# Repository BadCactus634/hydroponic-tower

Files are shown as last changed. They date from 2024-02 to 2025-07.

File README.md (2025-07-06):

ENGLISH USERS [READ HERE](english.md)!

ATTENZIONE!! AGGIORNAMENTO CIRCUITO: Il convertitore DC-DC va messo PRIMA del relè, altrimenti l'ESP si riavvierà quando quest'ultimo scatta. Questo a causa di un momentario undervoltage che si può correggere inserendo un condensatore.

# Serra idroponica
Crea una serra idroponica stampata in 3D con Arduino/ESP32!  



## Overview
Questa serra idroponica modulare è stata interamente stampata in 3D utilizzando del [PLA della PolyTerra](https://amzn.eu/d/4JCfyR1). Per stampare i pezzi marroni ho utilizzato poco meno di 1kg di filamento, mentre per quelli verdi circa 400g.  
C'è da dire però che **non ho avuto stampe fallite** e che **tutti i modelli sono stati ridotti del 10%** perché non ci stavano sul piatto della mia stampante (Flsun Q5).  
Se non l'hai ancora fatto, clicca qui (WIP!) per vedere il video che ho fatto dove mostro la serra in generale e spiego come l'ho costruita.

Questi sono alcuni dei componenti stampati:  

 <br>

Lista della spesa:
- 1kg filamento marrone
- 1kg filamento verde
- stampante 3D (ovviamente)
- pompa 12V
- ESP32/Arduino (qualsiasi)
- sensore di livello dell'acqua
- un vaso (se non è presente nei modelli già fatti, devi crearti un modello del coperchio su misura)
- nutrimento per coltivazioni idroponiche
- piantine da mettere nella serra
- step-up 5V-12V
- potenziometro, cavi, LED
 
Opzionale:
- millefori, stagno, stagnatore
- sensori per pH, CE e temperatura dell'acqua (io non li ho usati)

## Modelli 3D
I modelli che ho utilizzato io e che vedi nel mio video li trovi tutti nella cartella **File STL utilizzati**, inclusa la scatoletta che contiene i componenti.  
Non c'è il file del coperchio del vaso perché l'ho costruito in legno, visto che il mio vaso aveva delle misure particolari.

Nel caso ti servissero puoi scaricare lo zip contenente i modelli originali cliccando [qui](https://t.me/makersITA/907372) (non ci sono più su Thingiverse).

## Circuito
ATTENZIONE!! IL CIRCUITO NON E' STABILE: Il convertitore DC-DC va messo PRIMA del relè, altrimenti l'ESP si riavvierà quando scatta il relè. Credo sia a causa di un momentario undervoltage. 

Il cuore di questo progetto è un semplicissimo **ESP32** che fa da timer che accende la pompa dell'acqua per 5 minuti e poi attende un tempo variabile (regolabile dal potenziometro) che può andare da 10 a 60 minuti.  
Ci sono due LED che indicano lo stato del sistema (verde acceso = pompa attiva; rosso lampeggiante = mancanza di acqua nel serbatoio).  
L'ESP32 attiva un relè tramite un transistor, e il relè a sua volta attiva uno step-up che converte i 5V dell'alimentazione a 12V per la pompa dell'acqua, accendendola.  
Lo step-up è stato collegato a valle del relè in modo da essere attivato solo quando la pompa deve essere alimentata, risparmiando qualche mA del circuito di conversione e allungando quindi la durata della batteria (anche se io lo alimento tramite un alimentatore a muro).  

  

Nella figura sotto è riportato lo schema del circuito.

***ATTENZIONE!! È importante collegare il potenziometro al pin 33 (che corrisponde all'ADC1) perchè se lo colleghiamo a uno dei pin dell'ADC2 non funzionerà l'integrazione con Arduino Cloud, visto che l'ADC2 non funziona se la scheda utilizza il WiFi.***  

Circuito_schema

## Codice
Il codice è nel file **Codice_SerraIdroponica.ino** e questo è il suo funzionamento di base:  
- C'è acqua nel serbatoio?  
  Allora se è passato il tempo di attesa (regolabile tramite potenziometro da 10min a 60min) attiva la pompa per 5min.
  Durante il tempo di attivazione della pompa (che funziona tramite millis) verifica ogni secondo se è ancora presente acqua nel serbatoio, altrimenti fermala.

## Integrazione con Arduino Cloud 
Se volete fare l'integrazione su Arduino Cloud dovete usare il codice nella cartella **Codice_ArduinoCloud** perché ci sono alcune modifiche rispetto al codice normale.
Inoltre, sempre su Arduino Cloud, vanno impostate le seguenti variabili:  

   

**ATTENZIONE**  
I pin in entrambe le versioni del codice e lo schema del circuito si riferiscono alla scheda ESP32. Se volete utilizzare un Arduino dovete modificare i pin nel codice e nel circuito.

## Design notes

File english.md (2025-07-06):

WARNING!! THIS CIRCUIT IS NOT STABLE: The DC-DC converter needs to be put BEFORE the relay, otherwise an undervoltage would occur, resetting the ESP. There is a need for a capacitor.

# Hydroponic tower
Create a 3D-printed hydroponic tower with Arduino/ESP32!  



## Overview
This hydroponic tower has been entirely 3D printed using [PolyTerra PLA](https://amzn.eu/d/4JCfyR1). In order to print the brown modules I used almost 1kg of filament, whereas for the green ones I used 400g.  
It has to be sayd tho, that I **haven't got any failed print** and **all models were reduced by 10%** because they won't fit in my printing plate (I have an Flsun Q5).  
You can see a video of me building it (WIP). Note: it's in italian.

These are some of the printed components:  

 <br>

Shopping list:
- brown filament 1kg
- green filament 1kg
- 3D printer (obiuvsly)
- 12V water pump
- ESP32/Arduino (any)
- water level sensor
- vase cover (if yours isn't in the premade models, you need to create one custom-made)
- water nutriments for hydroponic based coltivations
- plants
- step-up 5V-12V
- potentiometer, cables, LEDs
 
Optional:
- prepboard, solder, soldering iron
- pH, CE and water temperature sensors (I haven't used them)

## 3D models
You can find all the models I used in the **File STL utilizzati** directory, including the box on which I putted the components.  
I haven't included the custom-made file for my vase cover because I builded it using wood.

If you need the original models, you can find them [here](https://t.me/makersITA/907372) (they aren't on Thingiverse anymore).

## Circuit
WARNING!! THIS CIRCUIT IS NOT STABLE: The DC-DC converter needs to be put BEFORE the relay, otherwise an undervoltage would occur, resetting the ESP. 

The heart of this project is a simple **ESP32** used as a timer, that turns on the water pump for 5 minutes and then waits a variable time that we can specify using the potentiometer (from 10 to 60 minutes).    
There are 2 LEDs that indicate the status of the system (green on = pump active; red blinking = no water).  
The ESP32 is connected to a relè via a transistor, the relè triggers a step-up that converts the 5V from the USB cable up to 12V for the water pump, thus turning it on.  
The step-up is connected after the relè, so it's only activated when the pump needs to be on, thus earning some mA for battery life, if you decide to power the system that way.  



You can see the circuit diagram in the picture below.  

***ATTENTION!! It's important to connect the potentiometer to pin 33 (which corresponds to ADC1) because if we were to connect it to any ADC2 pin, the integration with Arduino Cloud won't work, as the ADC2 doesn't work if the board is using WiFi.***

Circuito_schema

## Code
The code is in the file **Codice_SerraIdroponica.ino** and this is it's base working scheme:  
- Is there any water in the vase?  
  Then if the wait time has expired, activates the pump for 5min.  
  During pump activation time (it works by using millis) verify every second if water is still present in the vase, if not, stop the pump and turn on the red LED.

## Arduino Cloud integration 
If you want to integrate Arduino Cloud, you need to use the code in the directory **Codice_ArduinoCloud** because the code needs to be modified a bit.  
You also need to setup those variables in Arduino Cloud:  

   
  
**ATTENTION**  
The pins in the code and in the circuit diagram refers to the ESP32 board. If you want to use an Arduino you need to edit them in the code and thus in the circuit.

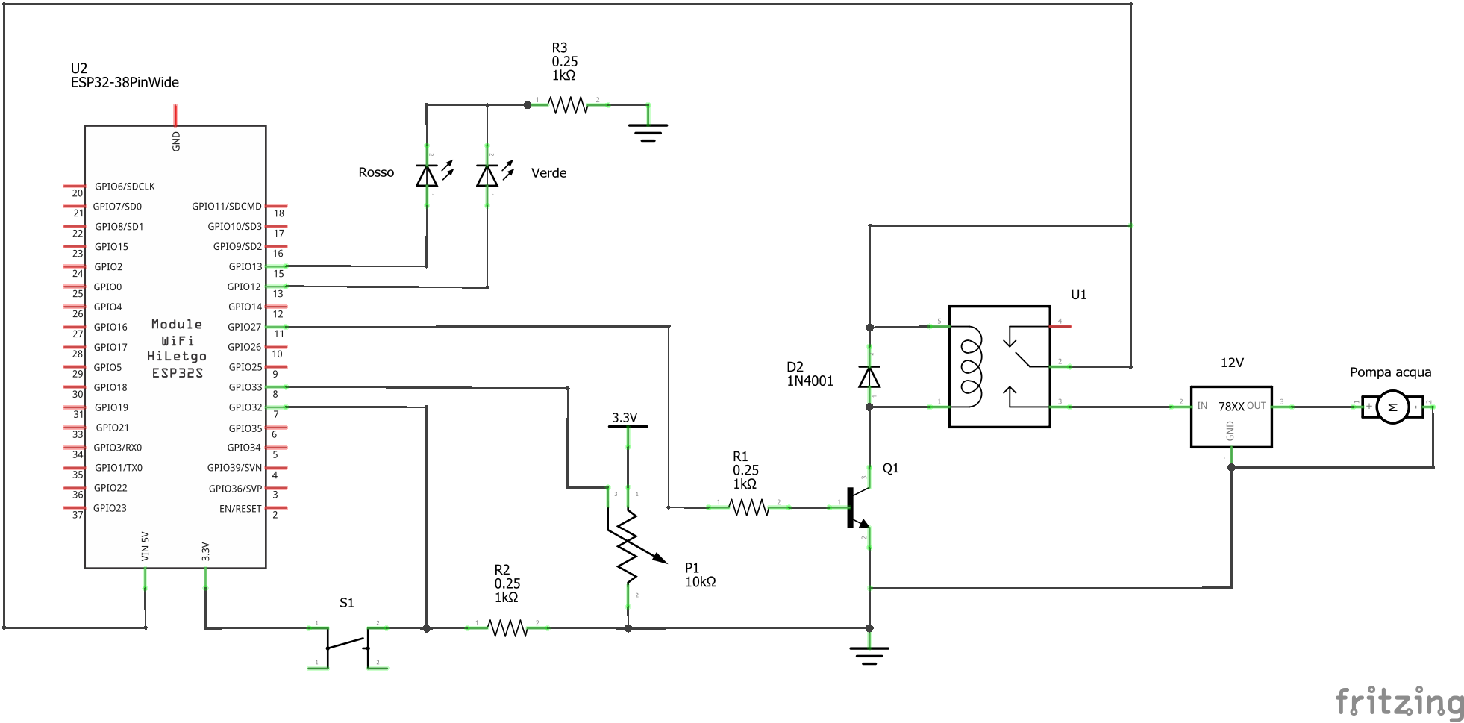
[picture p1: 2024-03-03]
Circuito_schema.png

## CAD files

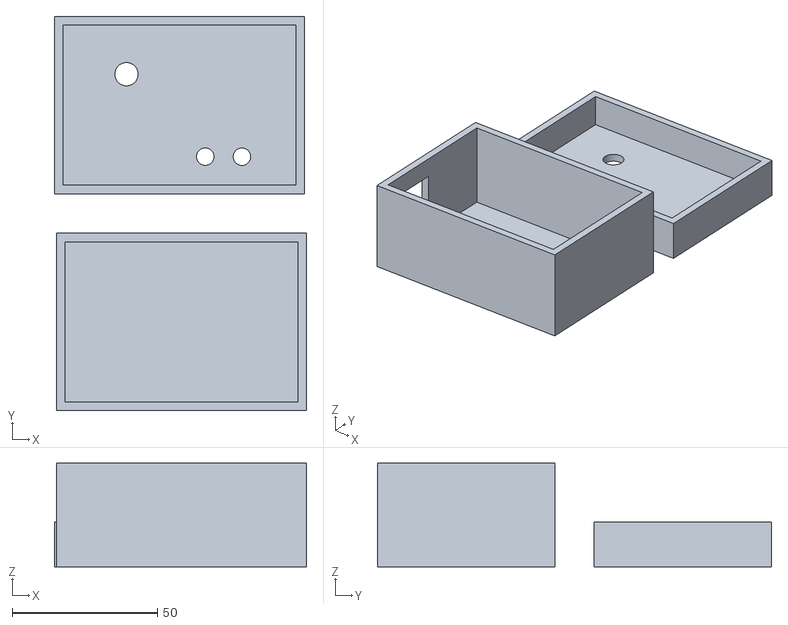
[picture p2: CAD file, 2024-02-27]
File STL utilizzati/Scatola componenti.stl
86.7 x 135.4 x 35.7

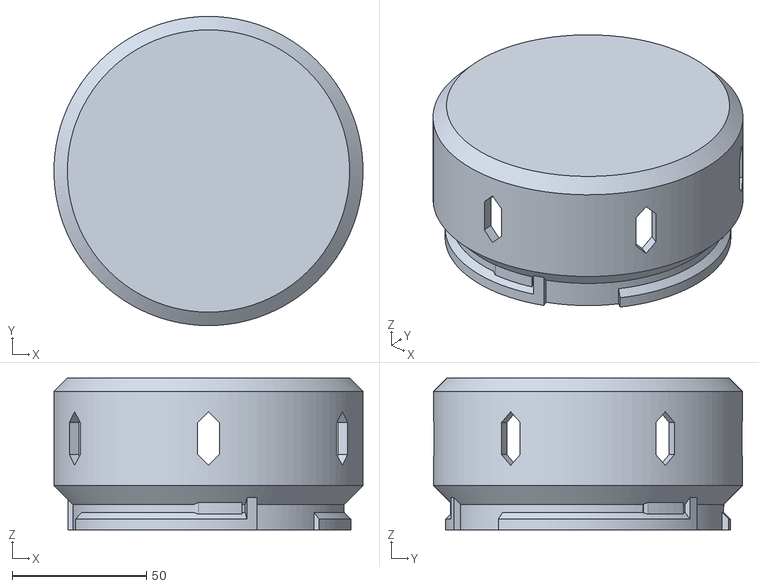
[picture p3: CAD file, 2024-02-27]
File STL utilizzati/Lid.STL
114.9 x 115.0 x 56.5

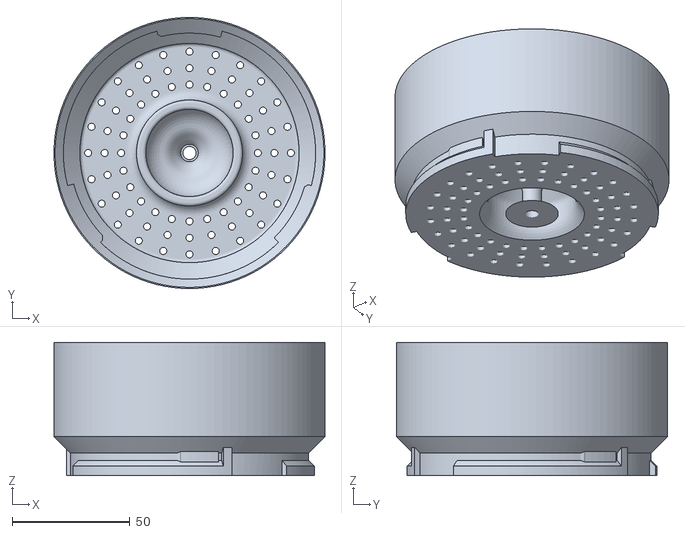
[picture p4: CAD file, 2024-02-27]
File STL utilizzati/Inserto superiore EU.stl
114.9 x 115.0 x 56.5

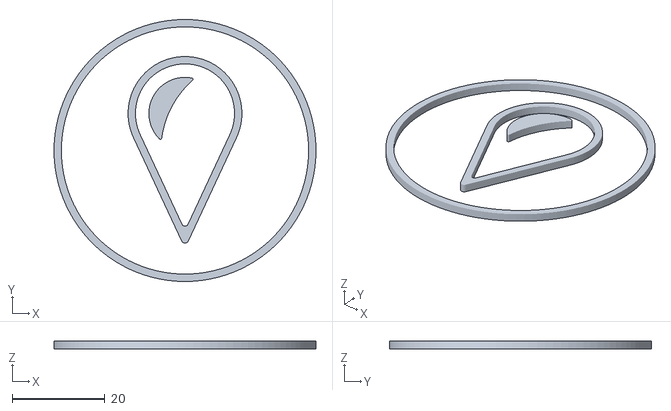
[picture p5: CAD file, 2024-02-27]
File STL utilizzati/Filling_Cap_Symbol.STL
56.6 x 56.6 x 1.70

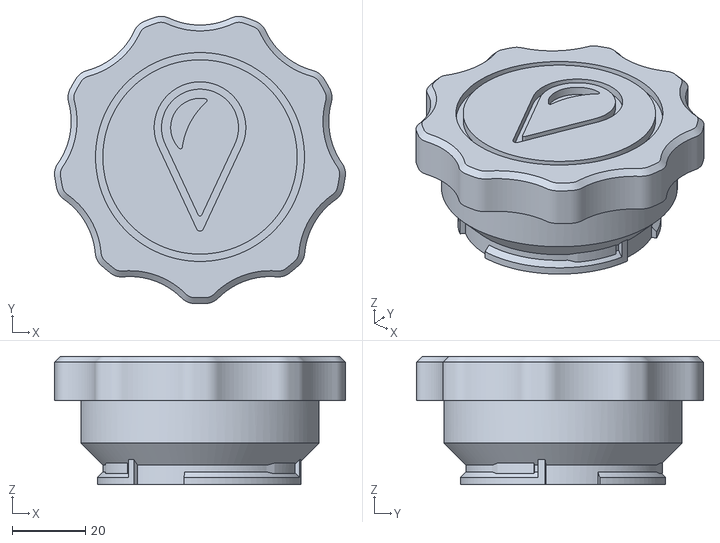
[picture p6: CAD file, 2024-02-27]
File STL utilizzati/Filling_Cap.STL
79.4 x 78.4 x 35.0

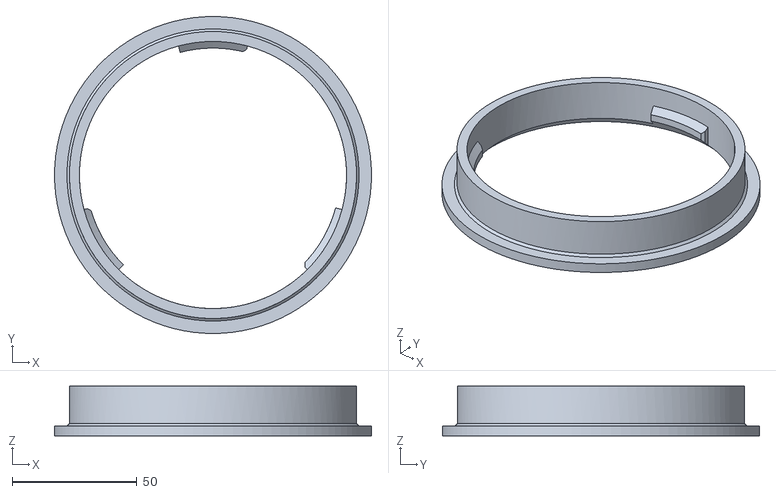
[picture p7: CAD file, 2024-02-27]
File STL utilizzati/Module_Adapter.STL
127.0 x 127.0 x 20.0

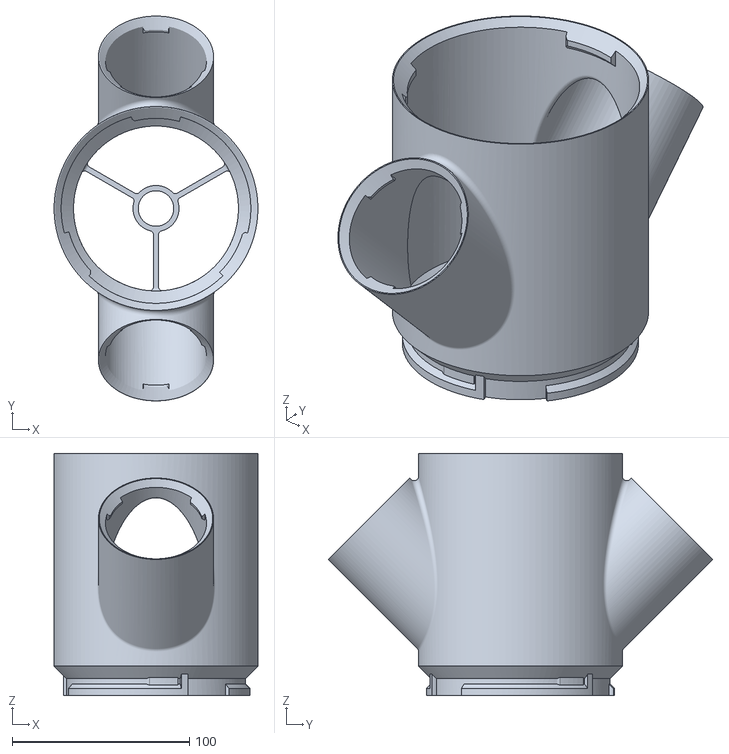
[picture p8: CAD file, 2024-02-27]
File STL utilizzati/2-Way_Planting_Module_Hollow_Opposite.STL
114.9 x 217.1 x 136.5

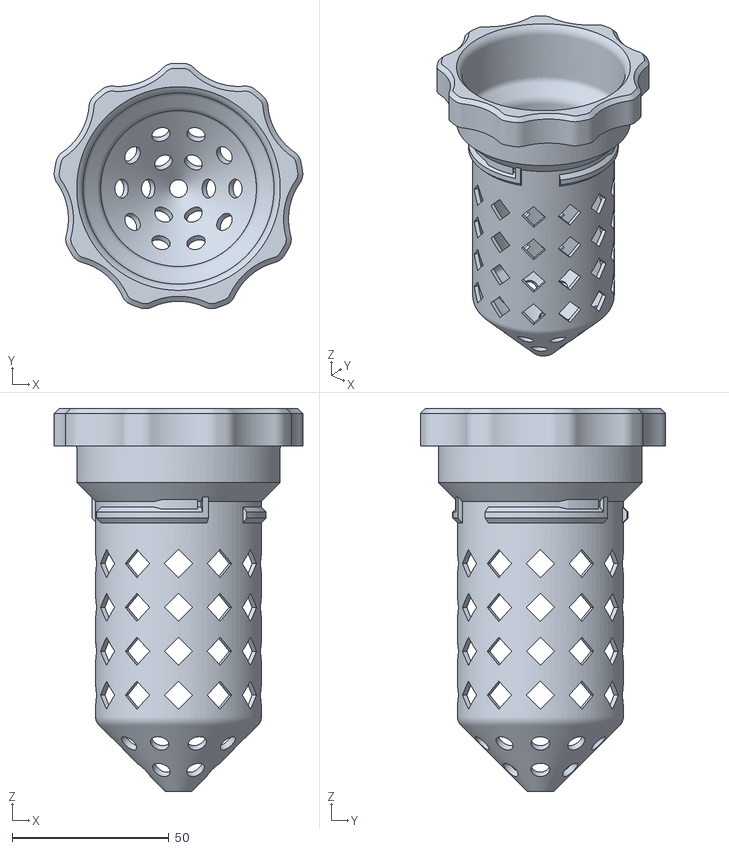
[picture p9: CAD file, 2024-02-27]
File STL utilizzati/Standard_Pot_02.STL
79.4 x 78.4 x 122.3

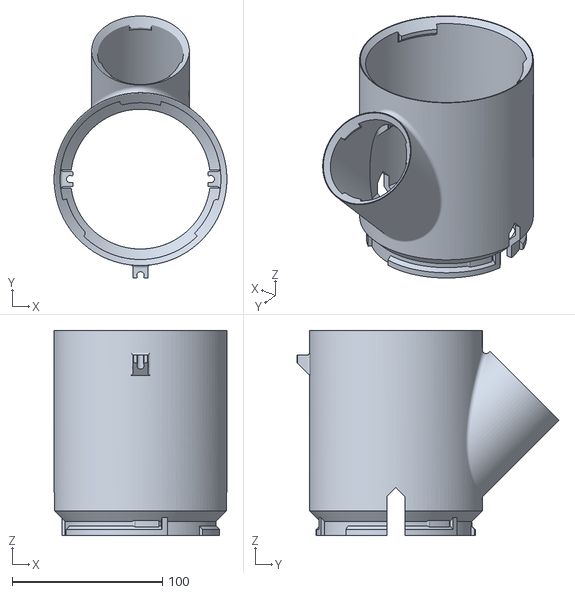
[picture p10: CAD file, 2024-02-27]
File STL utilizzati/Filling_Module_Cut_mod_01.STL
115.0 x 174.3 x 136.5

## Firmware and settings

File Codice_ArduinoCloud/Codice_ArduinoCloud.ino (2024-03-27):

#include "thingProperties.h"

int sensore = 32; // Sensore
int pompa = 27; // Pompa
int ledV = 12; // LED verde
int ledR = 13; // LED rosso
int potenziometro = 33, pausa = 0, nuovaPausa = 0;
bool halt;

unsigned long vecchioMillis, nuovoMillis, nuovoMillisHalt, vecchioMillisHalt;

// Temporizzazioni
int minuto = 60000; // Durata di 1 minuto (default: 60000)

// int tPompa = 5; // La pompa si accenderà per questo numero di minuti
int tMin = 10;
int tMax = 60;

void setup() {
  // Initialize serial and wait for port to open:
  Serial.begin(9600);
  // This delay gives the chance to wait for a Serial Monitor without blocking if none is found
  delay(1500); 

  // Defined in thingProperties.h
  initProperties();

  // Connect to Arduino IoT Cloud
  ArduinoCloud.begin(ArduinoIoTPreferredConnection);
  
  setDebugMessageLevel(2);
  ArduinoCloud.printDebugInfo();
  
  
  pinMode(sensore, INPUT);
  pinMode(pompa, OUTPUT);
  pinMode(ledV, OUTPUT);
  pinMode(ledR, OUTPUT);

  digitalWrite(ledV, LOW);
  digitalWrite(ledR, LOW);
  digitalWrite(pompa, LOW);
  
  pausa = analogRead(potenziometro);
  delay(100); // Delay per ADC
  pausa = map(pausa, 0, 4095, tMin, tMax);
  tempoRimanenteHalt = pausa;
  
  delay(2000);
  
  vecchioMillis=millis();
  tPompa = 5;
}

void loop() {
  ArduinoCloud.update();
  
  nuovaPausa = analogRead(potenziometro);
  delay(100); // Delay per ADC
  nuovaPausa = map(nuovaPausa, 0, 4095, tMin, tMax);

  if(nuovaPausa!=pausa){
    pausa=nuovaPausa;
    tempoRimanenteHalt = pausa;
  }
  
  if(digitalRead(sensore)) { // Se c'è acqua
      presenzaAcqua=true;
      
      if(!halt)
        controlloPompa();
    
  } else { // Se non c'è acqua
    vecchioMillis = millis();
    halt=false;
    timerPompa = 0;
    digitalWrite(pompa, LOW);
    digitalWrite(ledV, LOW);
    statoPompa=false;
    presenzaAcqua=false;
    
    
    digitalWrite(ledR, HIGH);
    delay(600);
    digitalWrite(ledR, LOW);
    delay(600);
  }
  
  delay(1000);
  
  if(halt){
    nuovoMillisHalt=millis();
    tempoRimanenteHalt = pausa - (nuovoMillisHalt - vecchioMillisHalt)/minuto;
    if(nuovoMillisHalt - vecchioMillisHalt >= pausa*minuto){
      halt=false;
      tempoRimanenteHalt = pausa;
      vecchioMillis = millis(); 
    }
  }
  
}


void controlloPompa(){
  nuovoMillis = millis();
  digitalWrite(pompa, HIGH);
  digitalWrite(ledV, HIGH);
  timerPompa = tPompa - (nuovoMillis - vecchioMillis)/minuto; // Tempo attività pompa rimanente
  statoPompa=true;

  if(nuovoMillis - vecchioMillis >= tPompa*minuto){ // Se è finito il tempo di attività della pompa
    digitalWrite(pompa, LOW);
    digitalWrite(ledV, LOW);
    timerPompa = 0;
    statoPompa = false;
    halt = true;
    vecchioMillisHalt=millis();
  }
}



/*
  Since TPompa is READ_WRITE variable, onTPompaChange() is
  executed every time a new value is received from IoT Cloud.
*/
void onTPompaChange()  {
  // Add your code here to act upon TPompa change
}

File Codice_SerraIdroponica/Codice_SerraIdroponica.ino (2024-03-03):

/* NATMUS
 *  by Stefano Rossi - 28/02/2024
 *  
 *  - Serra idroponica -
 *  questo codice non include la gestione dei sensori di parametri
 *  avanzati dell'acqua (pH, CE, temperatura)
 *  
 */

int sensore = 32; // Sensore
int pompa = 27; // Pompa
int ledV = 12; // LED verde
int ledR = 13; // LED rosso
int potenziometro = 33, pausa = 0, nuovaPausa = 0;

unsigned long vecchioMillis = 0;
unsigned long nuovoMillis = 0;

// Temporizzazioni
int minuto = 60000; // Durata di 1 minuto (default: 60000)

int tPompa = 5; // La pompa si accenderà per questo numero di minuti
int tMin = 10;
int tMax = 60;

void setup() {
  Serial.begin(9600);
  pinMode(sensore, INPUT);
  pinMode(pompa, OUTPUT);
  pinMode(ledV, OUTPUT);
  pinMode(ledR, OUTPUT);

  digitalWrite(ledV, LOW);
  digitalWrite(ledR, LOW);
  digitalWrite(pompa, LOW);

  Serial.println("Configurazione avvenuta");
  
  pausa = analogRead(potenziometro);
  delay(100); // Delay per ADC
  pausa = map(pausa, 0, 4095, tMin, tMax);
  Serial.println("Tempo: " + String(pausa) + "min");
  
  delay(2000);
}

void loop() {
  nuovaPausa = analogRead(potenziometro);
  delay(100); // Delay per ADC
  nuovaPausa = map(nuovaPausa, 0, 4095, tMin, tMax);

  if(nuovaPausa!=pausa){
    pausa=nuovaPausa;
    Serial.println("Nuovo tempo di attesa: " + String(pausa) + "min");
  }
  
  if(digitalRead(sensore)) { // Se c'è acqua
    nuovoMillis = millis();
    
    digitalWrite(pompa, HIGH);
    digitalWrite(ledV, HIGH);
    Serial.println("Pompa accesa");

    if(nuovoMillis - vecchioMillis >= tPompa*minuto){
      digitalWrite(pompa, LOW);
      digitalWrite(ledV, LOW);
      Serial.println("Pompa spenta");
      
      delay(pausa*minuto);
      nuovoMillis = millis();
      vecchioMillis = nuovoMillis;
    }
    
  } else {
    digitalWrite(pompa, LOW);
    digitalWrite(ledV, LOW);
    
    Serial.println("ATTENZIONE! Riempire serbatoio");
    
    while(!digitalRead(sensore)){ // Se non c'è acqua ripeti all'infinito
    digitalWrite(ledR, HIGH);
    delay(600);
    digitalWrite(ledR, LOW);
    delay(600);
    }
  }
  
  delay(1000);
}
